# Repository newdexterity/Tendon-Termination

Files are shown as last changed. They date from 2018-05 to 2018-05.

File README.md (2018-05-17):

# Ratchet Clutch Mechanism

**Title:** A Compact Ratchet Clutch Mechanism for Fine Tendon Termination and Adjustment

**Description:** 
<p align="justify">Adaptive, underactuated and compliant robot systems have received an increased interest over the last decade. Possible applications of these systems range from the development of adaptive robot hands to tendon-driven, soft exosuits. Despite the significant progress in the field, some basic design issues such as the tendon termination and adjustment have not yet been addressed properly. In this paper, we focus on tendon-driven, underactuated systems and we propose a compact ratchet clutch mechanism that facilitates a fine tendon termination and adjustment. The proposed mechanism is experimentally compared with six common tendon termination solutions, using two different tests: i) an accuracy test to verify how precisely each mechanism can adjust the tendon length and ii) a tensile test to derive the strength limit of each mechanism. The experiments validate that the ratchet clutch system is a precise and robust mechanism that outperforms all the solutions compared. A cable driven finger was designed and built to accommodate the proposed mechanism and test its efficiency and applicability to devices that require compactness (e.g., adaptive robot hands). The design of the mechanism is disseminated in an open-source manner. </p>  



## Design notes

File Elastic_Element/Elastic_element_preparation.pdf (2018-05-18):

## Elastic Element Preparation Instructions

In order to fabricate the elastic element, you should ensure you have the PMC-780 urethane rubber (parts A and B) and that you have 3D printed the following files: Mold_base.stl and Mold.stl.

1. Preparation – The PMC-780 has a limited shelf life and should be used as soon as

possible. Materials should be stored and used at room temperature (73°F/23°C).

Humidity should be low. Wear safety glasses, long sleeves and rubber gloves to

minimize contamination risk. Good ventilation is necessary.

2. Measuring & Mixing - Liquid urethanes are moisture sensitive and will absorb

atmospheric moisture. Mixing tools and containers should be clean and made of metal

or plastic. Pre-mix the Part B before using. After dispensing the required amounts of

Parts A and B into mixing container, mix thoroughly for at least 3 minutes making sure that you scrape the sides and bottom of the mixing container several times.

3. Removing bubbles - Although this product is formulated to minimize air bubbles in the

cured rubber, vacuum degassing will further reduce entrapped air. A pressure casting

technique using a pressure chamber can yield totally bubble free castings.

4. Assembly – Assembly the parts of the 3D printed mold before pouring the mixture

(ensure you have 3D printed the files Mold_base.stl and Mold_hole.stl).

5. Pouring - Pour your mixture in a single spot at the lowest point of the containment

field. Let the rubber seek its level up and over the model. A uniform flow will help

minimize entrapped air. The liquid rubber should level off at least 1.3 cm over the

highest point of the model surface.

6. Curing - Allow the mold to cure (at least 48 hours) at room temperature (73°F/23°C) before demolding. Do not cure rubber in temperatures less than 65°F/18°C.
7. Finishing – Remove the top piece of the mold and remove the elastic element. Trim

the edges of the elastic element to fit in your part. Use a small amount of superglue

to glue the elastic element to the base of your mechanism.

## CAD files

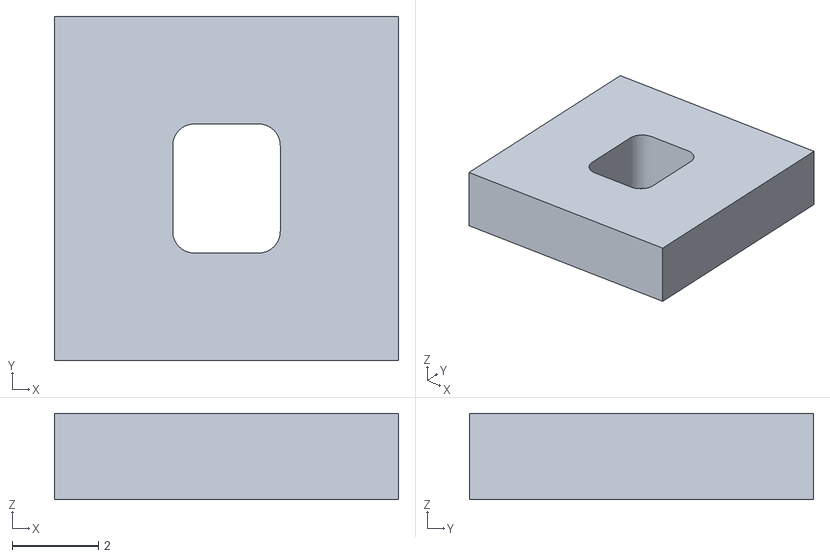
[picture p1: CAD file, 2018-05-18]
Elastic_Element/Mold.stl
8.00 x 8.00 x 2.00

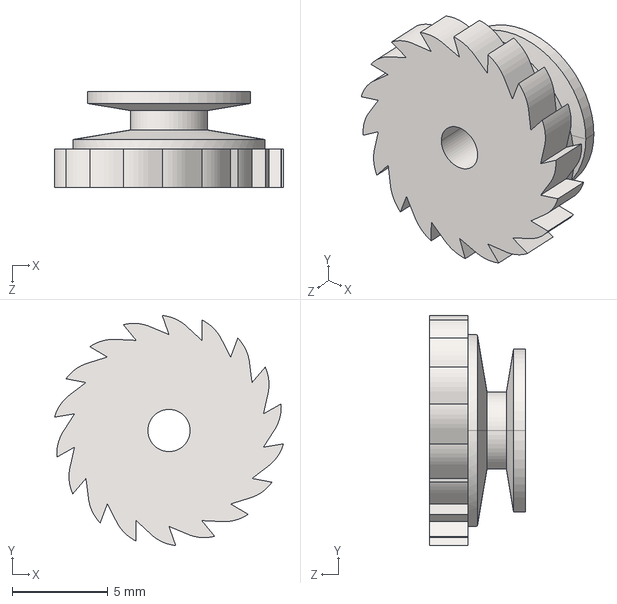
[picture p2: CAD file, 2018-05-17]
Pulley/Pulley.STEP
11.9 x 12.0 x 5.00 mm

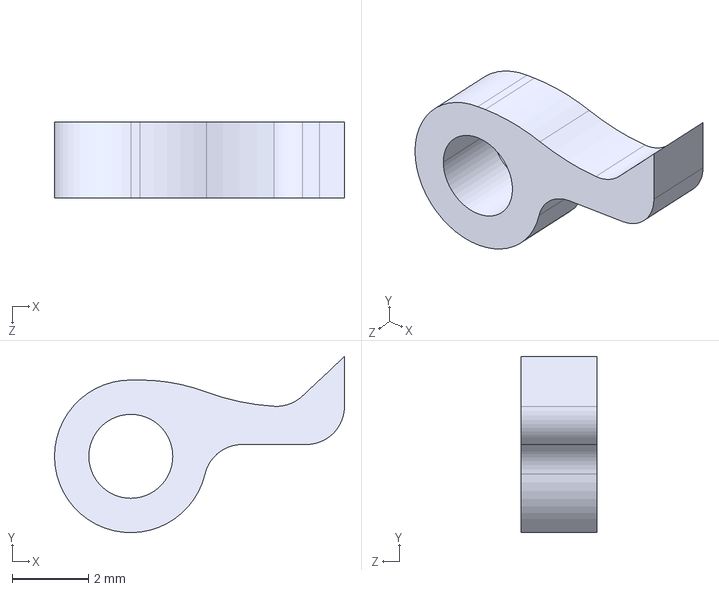
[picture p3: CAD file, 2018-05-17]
Ratchet/Ratchet.STEP
7.60 x 4.62 x 2.00 mm

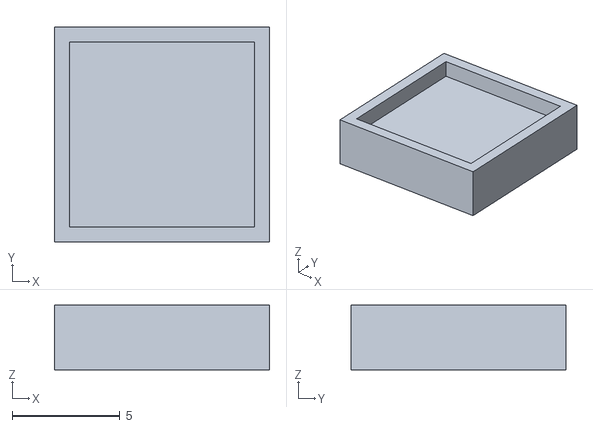
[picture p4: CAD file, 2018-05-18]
Elastic_Element/Mold_base.STL
10.0 x 10.0 x 3.00

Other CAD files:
Pulley/Pulley.DWG
Pulley/Pulley.IGS
Ratchet/Ratchet.DWG
Ratchet/Ratchet.IGS

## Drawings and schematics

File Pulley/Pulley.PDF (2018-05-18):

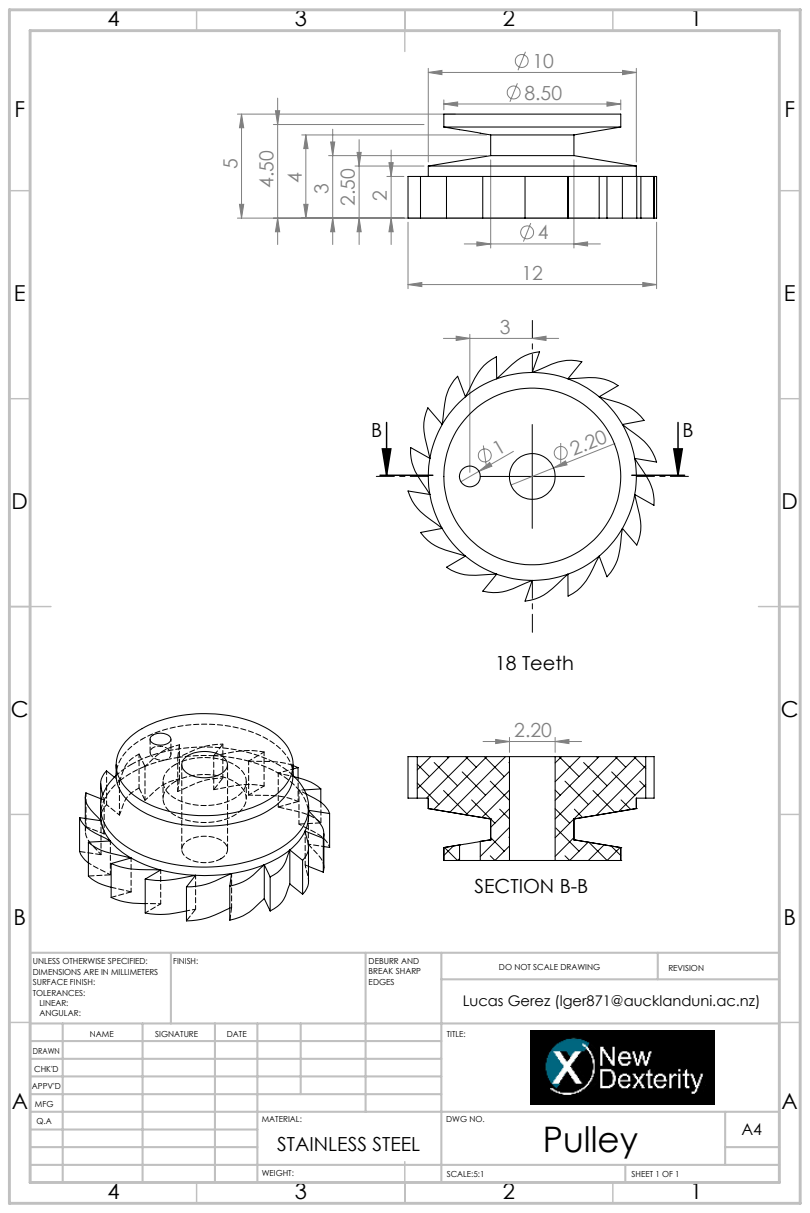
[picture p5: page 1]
SECTION B-B; 18 Teeth; FINISH:; DEBURR AND; BREAK SHARP; DO NOT SCALE DRAWING; REVISION; SCALE:5:1; SHEET 1 OF 1

UNLESS OTHERWISE SPECIFIED:
DIMENSIONS ARE IN MILLIMETERS
SURFACE FINISH:
TOLERANCES:
LINEAR:
ANGULAR:

Lucas Gerez (lger871@aucklanduni.ac.nz)

NAME | SIGNATURE | DATE | | | | TITLE:

DRAWN
CHK'D
APPV'D
MFG
Q.A | | | | MATERIAL: STAINLESS STEEL | DWG NO. Pulley | A4

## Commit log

2018-05-17 Added the files of the mechanism
    [Pulley.DWG, Pulley.IGS, Pulley.STEP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]
2018-05-18 Uploaded the mold file for the elastic part
    [Mold.stl, Mold_Support.stl]
